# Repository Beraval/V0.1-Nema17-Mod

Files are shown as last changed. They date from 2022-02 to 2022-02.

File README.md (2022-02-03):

# V0.1 Nema17 A/B Drive
**Not Compatible with the tophat**
This mod edits the A/B drives on the Voron V0.1 to allow for top-mounted nema17 motors.

## Why you should use nema17s instead of nema14s
TLDR: You shouldn't.
There is only one reason to run this mod and that is if you are trying to speed boat race. If that is not something that interests you this mod should not be installed on your machine. There will be no performance and/or quality increase from this mod under normal printing conditions. The stock nema14s will get you to speeds that will outperform the stock extrusion rate and stock cooling ability of the V0. This mod should only be considered if the motors are the bottleneck in your system and you need/want to go faster. Please see my list of reasons why to use/not use the mod below. If you decide you do not want to install this mod I also provided some alternative methods to increase the max speed of your system. 

### When to use this mod
- Your machine can extruder at a faster rate than your printer can run at
- Your cooling solution is outperforming my current speeds you print at
- I fit the above two conditions and I still want to go faster

### When not to use this mod
- Your machine can't extrude fast enough at the max speed with nema14s
- Your machine has problems with cooling at the max speed with nema14s
- You have not reached the limits with your current setup
- You use this machine for abs and need it to be fully enclosed (Tophat is not compatible with this mod)

## Other ways to reach faster speeds
- Increase the current on your motors
    - Please be aware of the currents your motors and stepper drivers are rated to. However, this is not the current that you will actually be able to use; it does not tell the whole story. You will run into overheating issues well before you hit the rated current. You can find more info elsewhere online if you want to learn more.
- Increase voltage of your motors
    - Please be aware of the voltage your components are rated to. Both your stepper drivers and controller boards need to be rated to the voltage you are running. The most common HV setup is 48v which will require 48v steppers drivers, a board with 48v sockets and a 48v psu. If your board/drivers are not up to spec they will instantly fry when you power on the machine and may start a fire. Additionally 48v is deadly and should be handled with the same precaution as mains power. Do not use 48v if you are not comfortable with it.  
- Decrease the weight of the moving mass
    - Since the V0 is a corexy machine this means decreasing the weight of the gantry. The first main way of doing this is replacing the aluminum extrusion with a carbon fiber one. Please be aware that cutting carbon fiber will release dangerous particulates into the air and proper protection must be used (your covid mask won't do anything). Also sufficient testing has not been done to fully understand the impact that this will have on rigidity and thermal warp due to heating the bimaterial gantry. It is believed that it will worsen both of these but there is not sufficient data to fully understand the degree it will do so. The second way to decrease weight is to move from a direct drive to a bowden system. However, this will obviously impact print quality negatively.

## BOM
##### Motors
The motors are the only additional parts that need to be bought as the hardware is the same as the stock V0. You can find the recommended motors below. I also recommend replacing your stepper drivers with something that can handle the current of larger motors. TMC2209s are only rated to 2 amps(can't go above 1.4 without cooling). I use 5160s for my stepper drivers.
##### Recommended Motors
- LDO-42STH47-2504AC
- NOC-17N18261A48MM-SJ

##### Printed Parts
You just need the six printed parts from the repo. You can use the normal tensioner nobs from the V0. The parts should be printed with the normal Voron part settings.

## Installation
The first thing you will need to do is remove the supports from the screw slots on the lower parts of the printed parts. After that the manual instructions can be followed for the most part. The only difference is that the motors will sit on top of the drives instead of the bottom.  Also the four screws that secure the drive to the frame should be put in place before attaching the motor. The motor will slightly block you from inserting them once it is attached.

## FAQ
Q: This is stupid nema14s provide more than enough power for such a small machine.
A: First of all thats not a question. Second of all I completely agree as I outlined multiple times above. This mod is only for speedboat racing. This mod will do nothing for you in normal printing conditions.

Q: Why are the motors on top of the a/b drives?
A: It was the only way to get them to fit without having a major overhaul to the frame/belt path. It also gives you more room for motor coolers and for extra/larger electronics on the back of the machine. The downside is that the tophat will no longer fit.

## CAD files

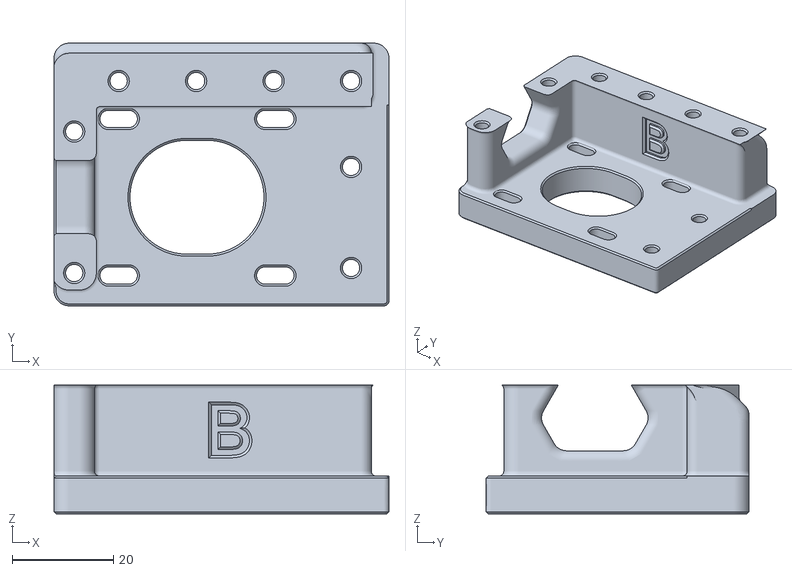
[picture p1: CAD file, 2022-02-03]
STL/B_Drive_Frame_Lower_x1.stl
66.3 x 52.0 x 25.5

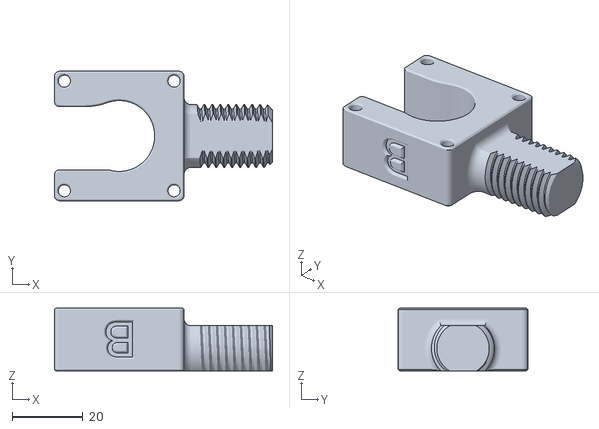
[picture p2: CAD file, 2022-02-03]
STL/[a]_B_Drive_Tensioner_x1.stl
61.6 x 36.6 x 17.8

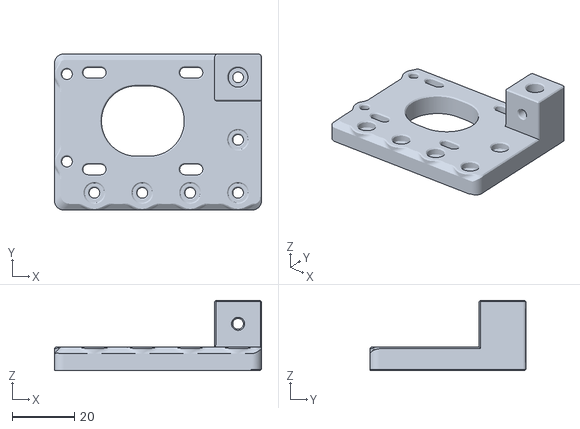
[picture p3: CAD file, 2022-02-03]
STL/A_Drive_Frame_Upper_x1.stl
66.3 x 50.0 x 22.5

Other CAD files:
STL/[a]_A_Drive_Tensioner_x1.stl
STL/A_Drive_Frame_Lower_x1.stl
STL/B_Drive_Frame_Upper_x1.stl
